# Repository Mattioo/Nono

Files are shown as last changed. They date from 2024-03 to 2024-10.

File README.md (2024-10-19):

# Nono - Prezentacja

Prezentacja  
[Zobacz wideo na YouTube](https://www.youtube.com/watch?v=TIbfDBwoEBU)

# 1. Wprowadzenie

## 1.1 Cel projektu

Ten projekt to zdalnie sterowany czołg RC oparty na Arduino Due, zaprojektowany do eksploracji terenów na duże odległości. Pojazd wykorzystuje technologię Crossfire (CRSF) do precyzyjnego sterowania oraz cyfrowy system wizyjny DJI, który pozwala na przesyłanie obrazu z ruchomej kamery do gogli DJI FPV V2, wzbogaconego o podstawowe informacje OSD (On-Screen Display) dzięki protokołowi MSP. W repozytorium znajdziesz wszystkie potrzebne informacje i kod do zbudowania tej konstrukcji. Projekt ma na celu umożliwienie dalekozasięgowej eksploracji ciekawych miejsc, z możliwością rejestrowania wizji z pokładu pojazdu. W przyszłości planuję publikować materiały wideo i bardziej szczegółowe opisy działania. Miłej zabawy! :)

## 1.2 Konfiguracja

* Zrootować gogle oraz air unit wykorzystując platformę WTFOS (https://fpv.wtf/) i zainstalować przez dostępny tam PackageManager pakiet msp-osd (dostępny również w repozytorium: [msp-osd-0.10.1.zip](External/msp-osd-0.10.1.zip)) na obu urządzeniach umożliwiając interpretacje komunikatów protokołu komunikacyjnego MSP.
* Włączyć w ustawieniach gogli opcję "Custom OSD".
* Doinstalować do Arduino IDE bibliotekę ReefwingMSP v. 2.0.0 (dostępną również w repozytorium: [Reefwing-MSP-main.zip](External/Reefwing-MSP-main.zip)).
* Skonfigurować Arduino IDE do pracy z Arduino Due:  
Tools -> Board -> Arduino SAM Boards(32-bits ARM Cortex-M3) -> Arduino Due (Programming Port).
* Wgrać na Arduino Due program przygotowany w pliku [Nono.ino](Nono.ino) (Należy odpiąć czujnik A02YYUW na czas wgrywania oprogramowania).
* Ustawić przy pomocy potencjometra na przetwornicy Buck napięcie wyjściowe dla złącza ADJ na +/- 7V.

# 2. Komponenty
## 2.1. Elementy konstrukcyjne

* Kadłub: WT-200 (złożona metalowa obudowa z silnikami, gąsienicami i wbudowanym oświetleniem bez elektroniki) ~2000 zł uwzględniając podatek  
https://www.ebay.com/itm/355056959871?itemid=355056959871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

* Uchwyt do serw: standard Pan/Tilt (x3) ~ 66 zł  
https://botland.com.pl/uchwyty-i-mocowania-do-serw/13500-uchwyt-do-serw-standard-pantilt-5904422358686.html

* Aluminiowy okrągły orczyk - 20mm / 6mm (x3) ~ 9 zł  
https://botland.com.pl/orczyki-do-serw/12538-aluminiowy-okragly-orczyk-20mm-6mm-5904422319533.html

* Górna część obudowy zaprojektowana w AutoCAD 2024 i wycięta laserem przez firmę AJMaker na podstawie przygotowanego projektu [Nono.dxf](External/Nono.dxf) ~ 350 zł  
https://ajmaker.pl/produkt/ciecie-laserem/

## 2.2. Elementy elektroniczne

* Wentylator 08025DA-12P-AA-00 [80x80x25] 12VDC (chłodzenie air unit - 75 CFM) ~ 110zł  
https://www.mouser.pl/ProductDetail/NMB-Technologies/08025DA-12P-AA-00?qs=byeeYqUIh0PE89S%2FBCp52A%3D%3D

*  Serwo Feetech FT6335M - standard (x3) ~ 330 zł  
https://botland.com.pl/serwa-typu-standard/17694-serwo-feetech-ft6335m-standard-5904422328474.html

* Buzzer z zasilaniem LiPo Iflight YR50B_S Finder Buzzer 100dB ~ 50 zł  
https://dronexpert.eu/buzzer-z-zasilaniem-lipo-iflight-yr50b-s-finder-buzzer-100db-p-14827.html

* Przetwornica Buck 3A wielokanałowa 3.3V 5V 12V ~ 35 zł  
https://allegro.pl/oferta/przetwornica-buck-3a-wielokanalowa-3-3v-5v-12v-14156675359

* Moduł przekaźnika Iduino - 1 kanał - styki 10A/250VAC - cewka 5V ~ 7 zł  
https://botland.com.pl/przekazniki-przekazniki-arduino/8228-modul-przekaznika-iduino-1-kanal-styki-10a250vac-cewka-5v-5903351241229.html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

* Czujnik napięcia 0-25V dzielnik 5V/25V ~ 4 zł  
https://allegro.pl/oferta/770-czujnik-napiecia-0-25v-dzielnik-5v-25v-arduino-13720748764

* Ultradźwiękowy czujnik odległości A02YYUW 3-450cm - wodoodporny - DFRobot SEN0311 ~ 105 zł  
https://botland.com.pl/ultradzwiekowe-czujniki-odleglosci/15717-ultradzwiekowy-czujnik-odleglosci-a02yyuw-3-450cm-wodoodporny-dfrobot-sen0311-5904422377984.html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

* DFRobot BTS7960 - dwukanałowy sterownik silników 35V/15A ~ 260 zł  
https://botland.com.pl/produkty-wycofane/2691-dfrobot-bts7960-dwukanalowy-sterownik-silnikow-35v-15a-5903351243001.html

* Cytron SC08A - sterownik serw 8-kanałowy - UART ~ 72 zł  
https://botland.com.pl/sterowniki-serw/12396-cytron-sc08a-sterownik-serw-8-kanalowy-uart-5904422319137.html

* Odbiornik TBS Crossfire Nano RX (SE) ~ 140 zł  
https://www.nobshop.pl/odbiornik-tbs-crossfire-nano-rx-se-p-1694.html

* Arduino Due ARM Cortex ~ 215 zł  
https://botland.com.pl/arduino-seria-podstawowa-oryginalne-plytki/1214-arduino-due-arm-cortex-a000062-7630049200487.html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

* Akumulator 6500mAh 11.1V 60C BASHING Gens Ace LiPo (x2) ~ 700 zł  
https://allegro.pl/oferta/akumulator-6500mah-11-1v-60c-bashing-gens-ace-lipo-14795865034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

* Nadajnik z kamerą Caddx Air Unit Polar starlight Digital HD DJI FPV system	~ 940 zł  
https://www.nobshop.pl/nadajnik-z-kamera-caddx-air-unit-polar-starlight-digital-hd-dji-fpv-system-p-2978.html

## 2.3. Elementy wyposażenia

* Gogle DJI FPV V2 ~ 3000 zł  
https://ironsky.pl/drony-sklep/produkt/dji-fpv-goggles-v2/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

* Kontroler TBS Tango 2 (Team Blackspeep) ~ 900 zł  
https://www.ebay.com/itm/145920613727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

## 2.4. Dodatkowe elementy

* 181 Radiator aluminiowy 9x9x5mm (x10) ~ 17 zł  
https://allegro.pl/oferta/181-radiator-aluminiowy-9x9x5mm-9382407076

* M4 NAKRĘTKA KWADRATOWA NISKA 562 OCYNKOWANA 10SZT (x2) ~ 4 zł  
https://allegro.pl/oferta/m4-nakretka-kwadratowa-niska-562-ocynkowana-10szt-13056354425

* M4x30 ŚRUBA SZEŚCIOKĄTNA NIERDZEWNA A2 933 (10) (x2) ~ 5 zł  
https://allegro.pl/oferta/m4x30-sruba-szesciokatna-nierdzewna-a2-933-10-14255374599

* Podkładki płaskie 720 sztuk stal nierdzewna M2-M12 ~ 45 zł  
https://allegro.pl/oferta/podkladki-plaskie-720-sztuk-stal-nierdzewna-m2-m12-12966456002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

* ZESTAW 440 ŚRUB 6-KĄTNE HEX ZE STALI NIERDZEWNEJ ~ 27 zł  
https://allegro.pl/oferta/zestaw-440-srub-6-katne-hex-ze-stali-nierdzewnej-16119291441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

* Zestaw nylonowych śrubek i podkładek dystansowych M3 - 180 elementów ~ 34 zł  
https://botland.com.pl/produkty-wycofane/13577-zestaw-nylonowych-srubek-i-podkladek-dystansowych-m3-180-elementow-5904422320973.html

* Przedłużacz do serw 45cm (x3) ~ 12 zł  
https://botland.com.pl/przewody-do-serw/1387-przedluzacz-do-serw-45cm-5904422350857.html

* Przewody połączeniowe żeńsko-męskie 30cm kolorowe - 50szt. ~ 30 zł  
https://botland.com.pl/przewody-polaczeniowe-zensko-meskie/1438-przewody-polaczeniowe-zensko-meskie-30cm-kolorowe-50szt-5904422349400.html

* Przewody połączeniowe męsko-męskie 30cm kolorowe - 50szt. ~ 28 zł  
https://botland.com.pl/przewody-polaczeniowe-mesko-meskie/1437-przewody-polaczeniowe-mesko-meskie-30cm-kolorowe-50szt-5904422356002.html

* XT90H komplet z osłonkami, konektor AMASS oryginał (x2) ~ 16 zł  
https://allegro.pl/oferta/xt90h-komplet-z-oslonkami-konektor-amass-oryginal-8186134922

# 3. Schemat połączeń

## 3.1. Akumulator 6500mAh 11.1V 60C BASHING Gens Ace LiPo 
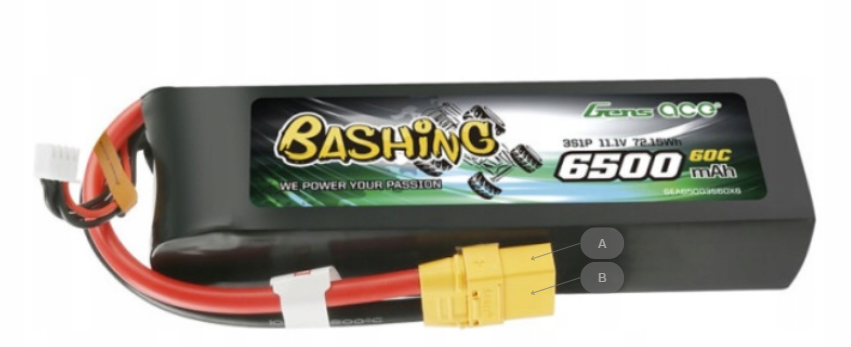
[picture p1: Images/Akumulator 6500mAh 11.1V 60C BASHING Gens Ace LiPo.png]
Akumulator 6500mAh 11.1V 60C BASHING Gens Ace LiPo


## 3.2. WT-200
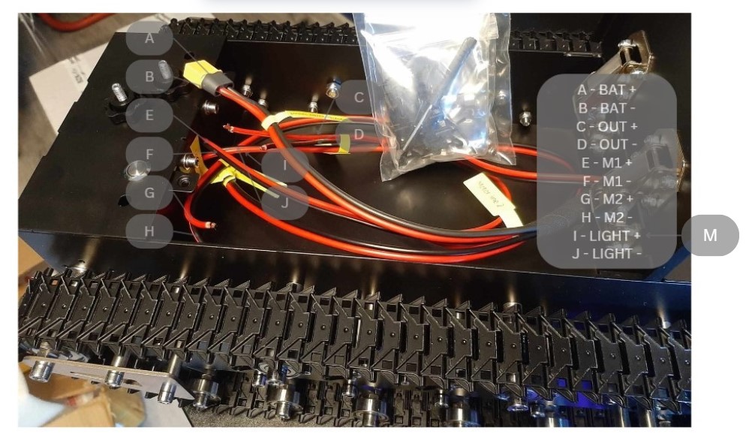
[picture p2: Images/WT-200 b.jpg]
WT-200


## 3.3. Przetwornica Buck 3A wielokanałowa 3.3V 5V 12V 
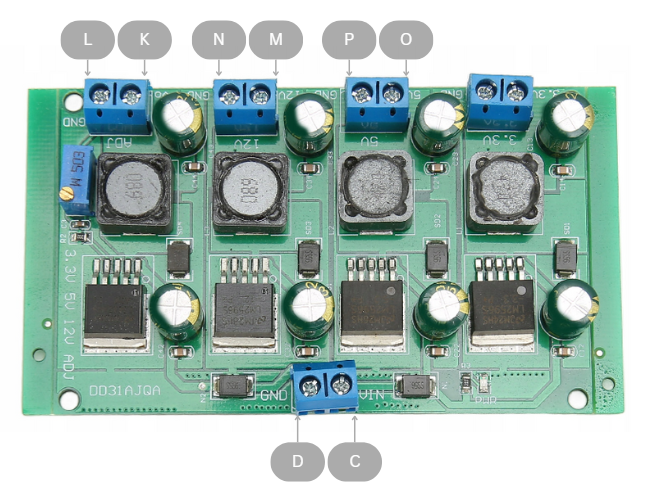
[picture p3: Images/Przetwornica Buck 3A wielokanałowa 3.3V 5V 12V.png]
Przetwornica Buck 3A wielokanałowa 3.3V 5V 12V


## 3.4. DFRobot BTS7960 - dwukanałowy sterownik silników 35V/15A
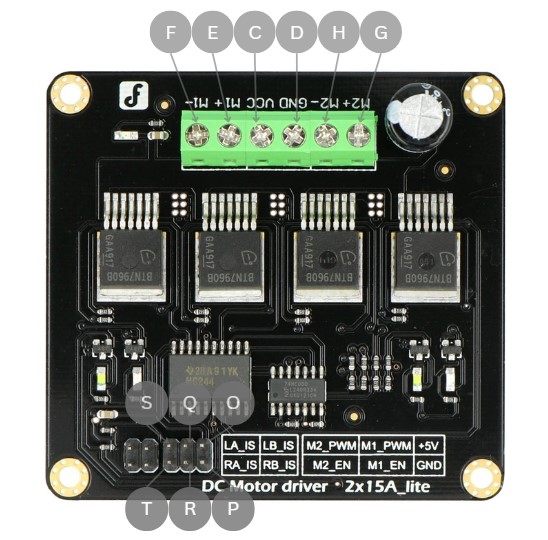
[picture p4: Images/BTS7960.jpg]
BTS7960


## 3.5. Cytron SC08A - sterownik serw 8-kanałowy - UART
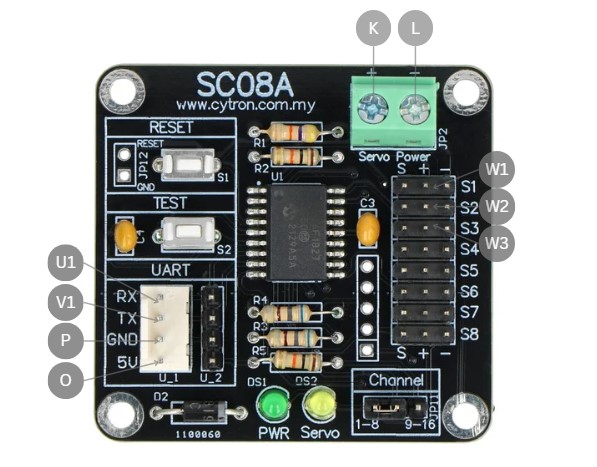
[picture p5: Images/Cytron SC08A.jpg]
Cytron SC08A


## 3.6. Serwo Feetech FT6335M - standard (x3)
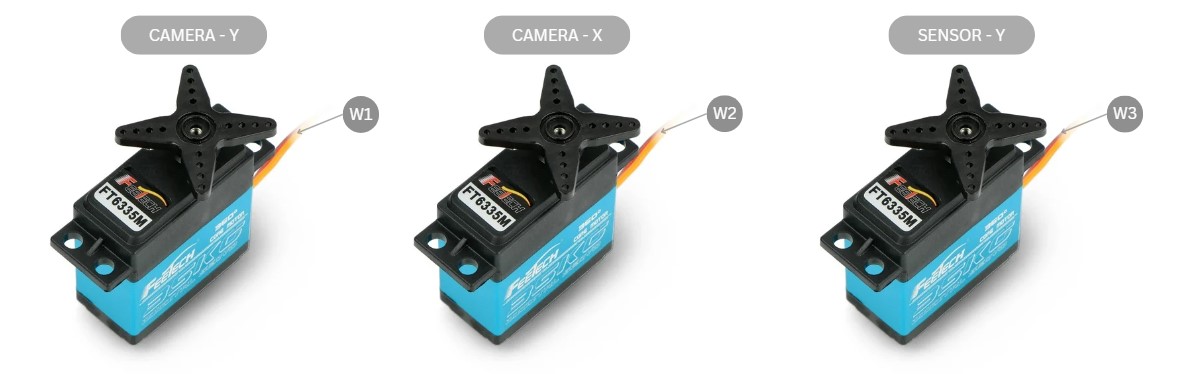
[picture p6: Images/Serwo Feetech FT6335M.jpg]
Serwo Feetech FT6335M


## 3.7. Nadajnik z kamerą Caddx Air Unit Polar starlight Digital HD DJI FPV system
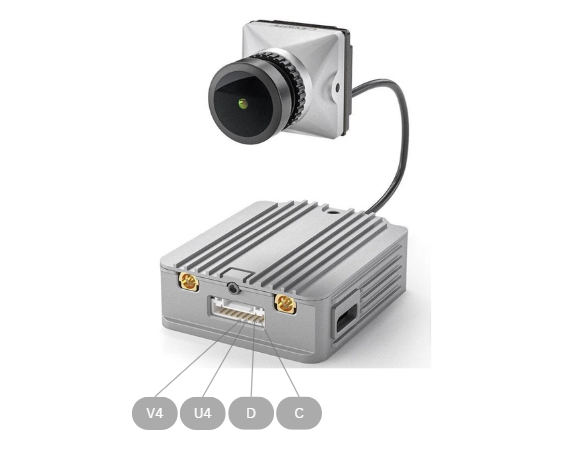
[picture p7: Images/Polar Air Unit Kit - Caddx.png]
Polar Air Unit Kit - Caddx


## 3.8. Odbiornik TBS Crossfire Nano RX (SE)
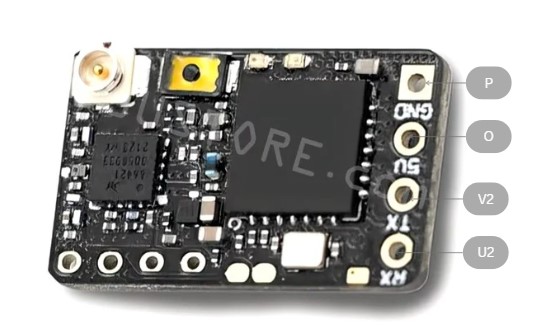
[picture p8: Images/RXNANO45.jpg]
RXNANO45


## 3.9. Ultradźwiękowy czujnik odległości A02YYUW 3-450cm - wodoodporny - DFRobot SEN0311
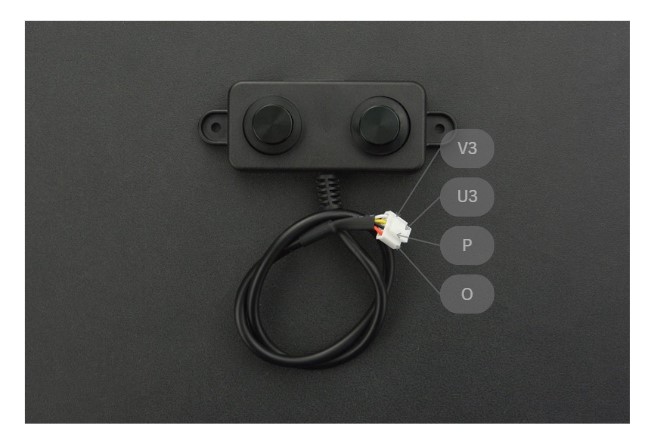
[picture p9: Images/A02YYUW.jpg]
A02YYUW


## 3.10. Buzzer z zasilaniem LiPo Iflight YR50B_S Finder Buzzer 100dB
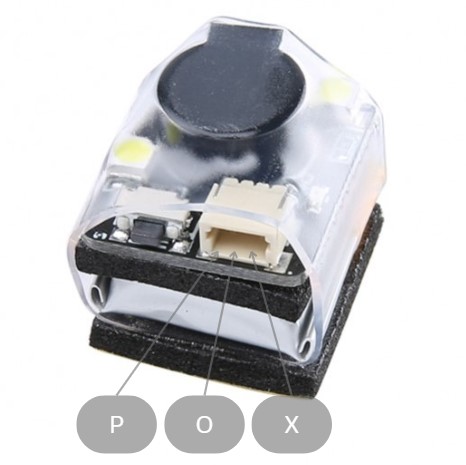
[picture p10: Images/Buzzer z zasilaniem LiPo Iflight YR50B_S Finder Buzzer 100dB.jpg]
Buzzer z zasilaniem LiPo Iflight YR50B_S Finder Buzzer 100dB


## 3.11. Moduł przekaźnika Iduino - 1 kanał - styki 10A/250VAC - cewka 5V
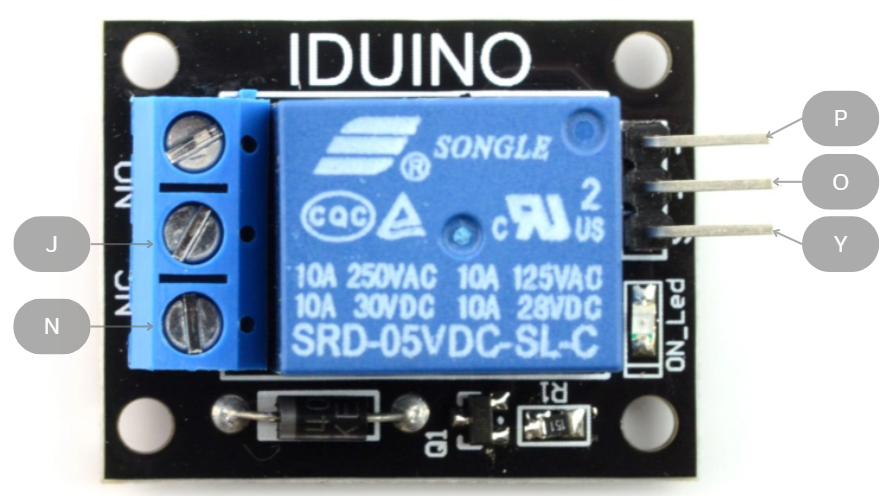
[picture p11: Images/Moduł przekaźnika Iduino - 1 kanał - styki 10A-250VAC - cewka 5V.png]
Moduł przekaźnika Iduino - 1 kanał - styki 10A-250VAC - cewka 5V


## 3.12. Czujnik napięcia 0-25V dzielnik 5V/25V
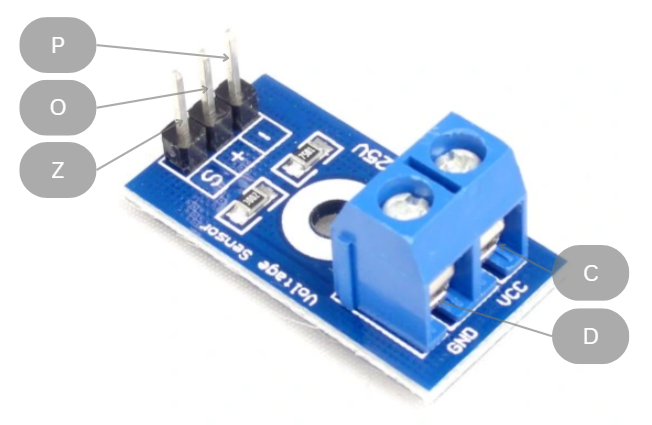
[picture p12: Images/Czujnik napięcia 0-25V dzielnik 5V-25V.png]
Czujnik napięcia 0-25V dzielnik 5V-25V


## 3.13. Wentylator 08025DA-12P-AA-00 [80x80x25] 12VDC
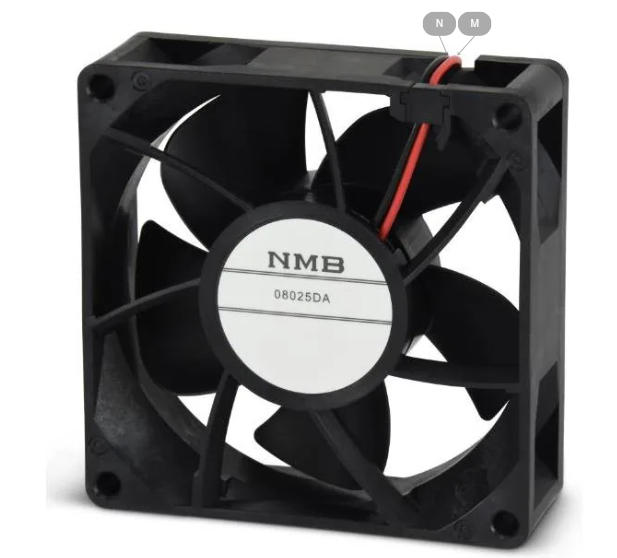
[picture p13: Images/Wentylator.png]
Wentylator


## 3.14. Arduino Due ARM Cortex
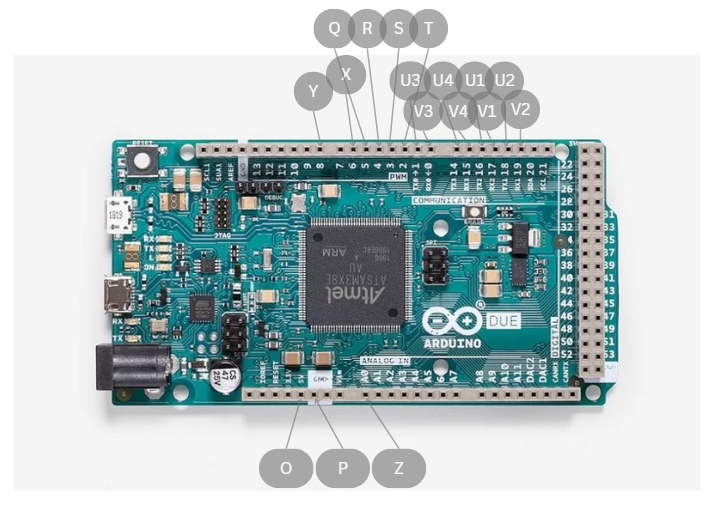
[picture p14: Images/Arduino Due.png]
Arduino Due


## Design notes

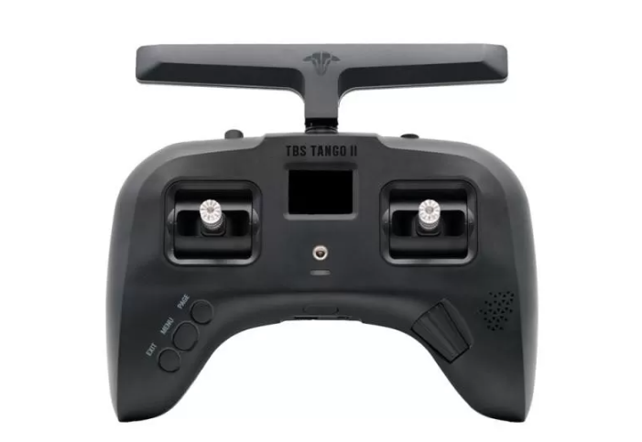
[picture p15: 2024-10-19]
Images/TBS Tango 2.png

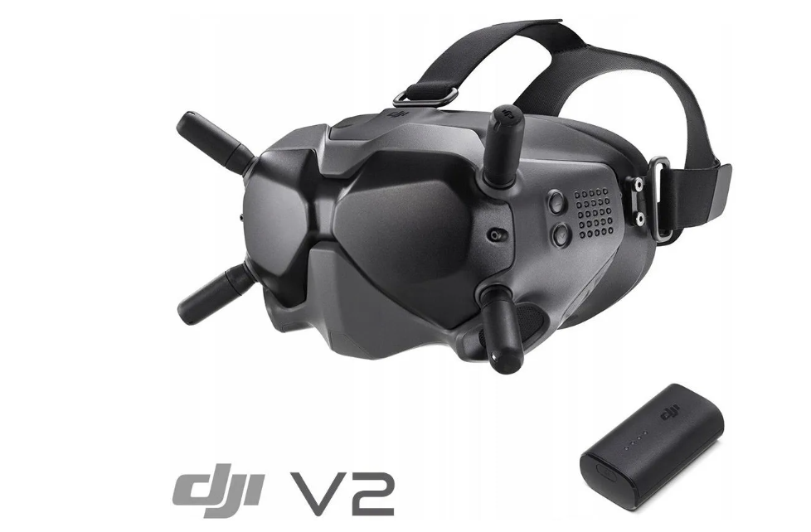
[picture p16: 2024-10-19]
Images/Dji Fpv Goggles V2.png

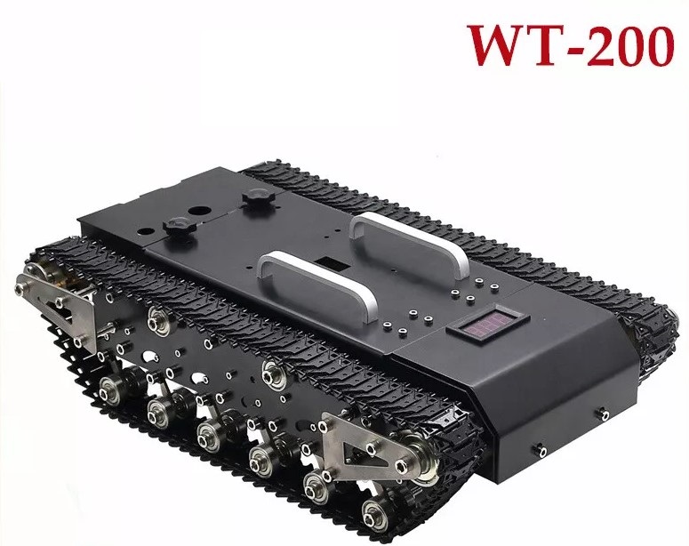
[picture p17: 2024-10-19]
Images/WT-200.jpg

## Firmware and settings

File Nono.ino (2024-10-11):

#include "RXNANO45.h"
#include "SC08A.h"
#include "A02YYUW.h"
#include "BTS7960.h"
#include "OSD.h"

#define BUZZER_PIN 6
#define LIGHT_PIN 8

std::vector<unsigned char> servo_channels = {1, 2, 3};

A02YYUW a02yyuw(Serial);
RXNANO45 rxnano45(Serial1);
SC08A sc08a(Serial2);
OSD osd(Serial3);
BTS7960 bts7960;

HardwareSerial* setup_logger(HardwareSerial* serial = nullptr) {
  if (serial != nullptr) {
    serial->begin(115200);
  }
  return serial;
}

void setup() {
  HardwareSerial* logger = setup_logger(); // setup_logger(&Serial);
  
  setup_outputs();  
  setup_rxnano45(logger);
  setup_sc08a(logger);
  setup_a02yyuw(logger);
  setup_bts7960(logger);
  setup_osd(logger);

  pinMode(LED_BUILTIN, OUTPUT);
}

void setup_outputs() {
  pinMode(BUZZER_PIN, OUTPUT);
  pinMode(LIGHT_PIN, OUTPUT);
}

void setup_rxnano45(HardwareSerial* logger) {
  rxnano45.set_logger(logger);
  rxnano45.init();
}

void setup_sc08a(HardwareSerial* logger) {
  sc08a.set_logger(logger);
  sc08a.set_channels(servo_channels);
  sc08a.set_input_range(CRSF_CHANNEL_VALUE_MIN, CRSF_CHANNEL_VALUE_MAX);
  sc08a.init();

  sc08a.home();
}

void setup_a02yyuw(HardwareSerial* logger) {
  a02yyuw.set_logger(logger);
  a02yyuw.init();
}

void setup_bts7960(HardwareSerial* logger) {
  bts7960.set_logger(logger);
  bts7960.set_pins(2, 3, 4, 5);
  bts7960.set_input_range(CRSF_CHANNEL_VALUE_MIN, CRSF_CHANNEL_VALUE_MID, CRSF_CHANNEL_VALUE_MAX, CRSF_CHANNEL_VALUE_OFF);
  bts7960.set_history_size(800);
  bts7960.set_mode(CRSF_CHANNEL_VALUE_MIN);
  bts7960.init();
}

void setup_osd(HardwareSerial* logger) {
  osd.set_logger(logger);
  osd.init(5000, 6500, 3, 10.5, 12.6);
}

void set_buzzer(bool isAlive) {
  digitalWrite(BUZZER_PIN, !isAlive ? LOW : HIGH);
}

void set_light(int signal) {
  digitalWrite(LIGHT_PIN, signal == CRSF_CHANNEL_VALUE_MAX ? HIGH : LOW);
}

bool set_distance_sensor(int signal) {
  return signal == CRSF_CHANNEL_VALUE_MAX;
}

float get_voltage() {
  const int numSamples = 10;
  int totalAnalogValue = 0;
  
  for (int i = 0; i < numSamples; i++) {
    totalAnalogValue += analogRead(A0);
    delay(5);
  }
  
  int averageAnalogValue = totalAnalogValue / numSamples;
  
  float measuredVoltage = (averageAnalogValue * 3.3) / 4095;
  return measuredVoltage * 5.0 * 4.2857;
}

void loop() {
  if (RXNANO45::IsAlive) {
    CrsfSerialState controller = rxnano45.get_state();

    if (RXNANO45::arm_state())
    {
      set_light(controller.A);
      bts7960.set_mode(controller.B);

      bts7960.movement(controller.Move_Y, controller.Move_X);

      bool setDistanceSensor = set_distance_sensor(controller.D);

      if (setDistanceSensor && sc08a.is_possible_movement_sensor(controller.Camera_Y)) sc08a.set_inverted({ servo_channels[2] }, controller.Camera_Y);
      else if (sc08a.is_possible_movement_Y(controller.Camera_Y)) sc08a.set({ servo_channels[0] }, controller.Camera_Y);
      if (sc08a.is_possible_movement_X(controller.Camera_X)) sc08a.set_inverted({ servo_channels[1] }, controller.Camera_X);
    }
  }
  else {
    sc08a.home();
    if (bts7960.can_reverse()) bts7960.reverse();
    else bts7960.stop();
  }

  if (!RXNANO45::IsInit)
    set_buzzer(RXNANO45::IsAlive);

  rxnano45.loop();
  a02yyuw.loop();

  osd.set_state(RXNANO45::arm_state(), get_voltage());
  osd.set_distance(a02yyuw.get_distance());
  osd.loop();
}

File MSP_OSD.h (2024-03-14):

#pragma once

#define MSP_CMD_OSD_CONFIG 84
#define MSP_CMD_FILTER_CONFIG 92
#define MSP_CMD_PID_ADVANCED 94
#define MSP_CMD_STATUS_EX 150
#define MSP_CMD_RTC 247

#include <stdint.h>

//////////////////////////////////////////////////////////////////////////////////////////////////////////////////////////////////////////
/// MSP_CMD_OSD_CONFIG
//////////////////////////////////////////////////////////////////////////////////////////////////////////////////////////////////////////

struct msp_cmd_osd_config_t {
    uint8_t  osdflags;
    uint8_t  video_system;
    uint8_t  units;
    uint8_t  rssi_alarm;
    uint16_t cap_alarm;
    uint8_t  old_timer_alarm;
    uint8_t  osd_item_count;
    uint16_t alt_alarm;
    uint16_t osd_rssi_value_pos;
    uint16_t osd_main_batt_voltage_pos;
    uint16_t osd_crosshairs_pos;
    uint16_t osd_artificial_horizon_pos;
    uint16_t osd_horizon_sidebars_pos;
    uint16_t osd_item_timer_1_pos;
    uint16_t osd_item_timer_2_pos;
    uint16_t osd_flymode_pos;
    uint16_t osd_craft_name_pos;
    uint16_t osd_throttle_pos_pos;
    uint16_t osd_vtx_channel_pos;
    uint16_t osd_current_draw_pos;
    uint16_t osd_mah_drawn_pos;
    uint16_t osd_gps_speed_pos;
    uint16_t osd_gps_sats_pos;
    uint16_t osd_altitude_pos;
    uint16_t osd_roll_pids_pos;
    uint16_t osd_pitch_pids_pos;
    uint16_t osd_yaw_pids_pos;
    uint16_t osd_power_pos;
    uint16_t osd_pidrate_profile_pos;
    uint16_t osd_warnings_pos;
    uint16_t osd_avg_cell_voltage_pos;
    uint16_t osd_gps_lon_pos;
    uint16_t osd_gps_lat_pos;
    uint16_t osd_debug_pos;
    uint16_t osd_pitch_angle_pos;
    uint16_t osd_roll_angle_pos;
    uint16_t osd_main_batt_usage_pos;
    uint16_t osd_disarmed_pos;
    uint16_t osd_home_dir_pos;
    uint16_t osd_home_dist_pos;
    uint16_t osd_numerical_heading_pos;
    uint16_t osd_numerical_vario_pos;
    uint16_t osd_compass_bar_pos;
    uint16_t osd_esc_tmp_pos;
    uint16_t osd_esc_rpm_pos;
    uint16_t osd_remaining_time_estimate_pos;
    uint16_t osd_rtc_datetime_pos;
    uint16_t osd_adjustment_range_pos;
    uint16_t osd_core_temperature_pos;
    uint16_t osd_anti_gravity_pos;
    uint16_t osd_g_force_pos;
    uint16_t osd_motor_diag_pos;
    uint16_t osd_log_status_pos;
    uint16_t osd_flip_arrow_pos;
    uint16_t osd_link_quality_pos;
    uint16_t osd_flight_dist_pos;
    uint16_t osd_stick_overlay_left_pos;
    uint16_t osd_stick_overlay_right_pos;
    uint16_t osd_display_name_pos;
    uint16_t osd_esc_rpm_freq_pos;
    uint16_t osd_rate_profile_name_pos;
    uint16_t osd_pid_profile_name_pos;
    uint16_t osd_profile_name_pos;
    uint16_t osd_rssi_dbm_value_pos;
    uint16_t osd_rc_channels_pos;
    uint8_t  osd_stat_count;
    uint8_t  osd_stat_rtc_date_time;
    uint8_t  osd_stat_timer_1;
    uint8_t  osd_stat_timer_2;
    uint8_t  osd_stat_max_speed;
    uint8_t  osd_stat_max_distance;
    uint8_t  osd_stat_min_battery;
    uint8_t  osd_stat_end_battery;
    uint8_t  osd_stat_battery;
    uint8_t  osd_stat_min_rssi;
    uint8_t  osd_stat_max_current;
    uint8_t  osd_stat_used_mah;
    uint8_t  osd_stat_max_altitude;
    uint8_t  osd_stat_blackbox;
    uint8_t  osd_stat_blackbox_number;
    uint8_t  osd_stat_max_g_force;
    uint8_t  osd_stat_max_esc_temp;
    uint8_t  osd_stat_max_esc_rpm;
    uint8_t  osd_stat_min_link_quality;
    uint8_t  osd_stat_flight_distance;
    uint8_t  osd_stat_max_fft;
    uint8_t  osd_stat_total_flights;
    uint8_t  osd_stat_total_time;
    uint8_t  osd_stat_total_dist;
    uint8_t  osd_stat_min_rssi_dbm;
    uint16_t osd_timer_count;
    uint16_t osd_timer_1;
    uint16_t osd_timer_2;
    uint16_t enabledwarnings;
    uint8_t  osd_warning_count;
    uint32_t enabledwarnings_1_41_plus;
    uint8_t  osd_profile_count;
    uint8_t  osdprofileindex;
    uint8_t  overlay_radio_mode;
} __attribute__ ((packed));

//////////////////////////////////////////////////////////////////////////////////////////////////////////////////////////////////////////
/// MSP_NAME
//////////////////////////////////////////////////////////////////////////////////////////////////////////////////////////////////////////

#define MAX_NAME_LENGTH 16u

struct msp_cmd_name_t {
    char craft_name[MAX_NAME_LENGTH + 1];
} __attribute__ ((packed));

//////////////////////////////////////////////////////////////////////////////////////////////////////////////////////////////////////////
/// MSP_CMD_FILTER_CONFIG
//////////////////////////////////////////////////////////////////////////////////////////////////////////////////////////////////////////

#define GYRO_LPF1_DYN_MIN_HZ_DEFAULT 250
#define GYRO_LPF2_HZ_DEFAULT 500

enum lowpassFilterType_e {
    FILTER_PT1 = 0,
    FILTER_BIQUAD,
    FILTER_PT2,
    FILTER_PT3,
};

enum gyroHardwareLpf_e {
    GYRO_HARDWARE_LPF_NORMAL,
    GYRO_HARDWARE_LPF_OPTION_1,
    GYRO_HARDWARE_LPF_OPTION_2,
    GYRO_HARDWARE_LPF_COUNT
};

struct msp_cmd_filter_config_t {
    uint8_t  gyro_lpf1_static_hz_u8;
    uint16_t dterm_lpf1_static_hz;
    uint16_t yaw_lowpass_hz;
    uint16_t gyro_soft_notch_hz_1;
    uint16_t gyro_soft_notch_cutoff_1;
    uint16_t dterm_notch_hz;
    uint16_t dterm_notch_cutoff;
    uint16_t gyro_soft_notch_hz_2;
    uint16_t gyro_soft_notch_cutoff_2;
    uint8_t  dterm_lpf1_type;
    uint8_t  gyro_hardware_lpf;
    uint8_t  unused01;
    uint16_t gyro_lpf1_static_hz_u16;
    uint16_t gyro_lpf2_static_hz;
    uint8_t  gyro_lpf1_type;
    uint8_t  gyro_lpf2_type;
    uint16_t dterm_lpf2_static_hz;
    uint8_t  dterm_lpf2_type;
    uint16_t gyro_lpf1_dyn_min_hz;
    uint16_t gyro_lpf1_dyn_max_hz;
    uint16_t dterm_lpf1_dyn_min_hz;
    uint16_t dterm_lpf1_dyn_max_hz;
    uint8_t  unused02;
    uint8_t  unused03;
    uint16_t dyn_notch_q;
    uint16_t dyn_notch_min_hz;
    uint8_t  rpm_filter_harmonics;
    uint8_t  rpm_filter_min_hz;
    uint16_t dyn_notch_max_hz;
    uint8_t  dterm_lpf1_dyn_expo;
    uint8_t  dyn_notch_count;
} __attribute__ ((packed));

//////////////////////////////////////////////////////////////////////////////////////////////////////////////////////////////////////////
/// MSP_CMD_PID_ADVANCED
//////////////////////////////////////////////////////////////////////////////////////////////////////////////////////////////////////////

enum tpaMode_e {
    TPA_MODE_PD,
    TPA_MODE_D
};

enum auto_profile_cell_count_e {
    AUTO_PROFILE_CELL_COUNT_STAY = 0,
    AUTO_PROFILE_CELL_COUNT_CHANGE = -1
};
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

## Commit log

2022-09-02 New version of Nono
    Controled by XF Nano 45 and Arduino Due without FC
2024-10-11 Add files via upload
    update voltage range for osd
